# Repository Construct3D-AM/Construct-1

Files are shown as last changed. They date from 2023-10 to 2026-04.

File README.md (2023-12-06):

# README: Usage Guidelines
## Introduction
Welcome to the CAD Files Repository hosted by SERAPH TECHNOLOGIES t/a CONSTRUCT3D. This repository contains a collection of CAD, slicer and firmware files intended for educational and personal development purposes. We appreciate your interest and support in our work.

## Usage Restrictions
## 1. Non-Commercial Use Only
The CAD files provided in this repository are for **personal, non-commercial use only.** These files are not to be used for any commercial purposes, including but not limited to manufacturing, selling, or distribution of the designs or products derived from these files.

## 2. No Rights Granted
Downloading or using these CAD files **does not grant any rights or licenses to the user.** All rights, including but not limited to copyright, intellectual property rights, and distribution rights, are reserved by SERAPH TECHNOLOGIES. Any use of these files must comply with the terms and conditions stated herein.

## 3. Personal Use Only
The intent of providing these CAD files is solely for **personal use and learning.** Users are encouraged to use these files to enhance their skills, knowledge, and understanding of the relevant fields. However, any commercial exploitation or use of these files beyond personal purposes is strictly prohibited.

## 4. Modification and Redistribution
While users are permitted to modify the CAD files for personal use, redistribution of the original files or any modified versions is not allowed. Sharing these files on any platform or through any medium without the explicit permission of SERAPH TECHNOLOGIES is prohibited.

## 5. Disclaimer
SERAPH TECHNOLOGIES provides these CAD files 'as is' without any warranties, either expressed or implied. The use of these files is at the sole risk of the user. SERAPH TECHNOLOGIES shall not be liable for any direct, indirect, incidental, or consequential damages arising out of the use or inability to use these files.

## Acknowledgment
By downloading and using these CAD files, the user acknowledges that they have read, understood, and agreed to comply with the usage guidelines outlined in this document.

## Contact Information
For any inquiries or permissions related to the use of these CAD files, please contact SERAPH TECHNOLOGIES at:

[admin@construct-3d.com]

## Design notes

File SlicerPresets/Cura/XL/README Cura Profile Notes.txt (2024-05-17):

Notes: This document is temporary until the next update of CURA which hopefully will include our printers, natively.

=====
== Cura Setup Information
=====

=== Cura Setup instructions
You are going to want to add a 'Custom FFF machine'. this can be added under the preferences tab and adding a 'Non-networked printer".
In the scroll tab available, look for the 'Custom' header, and inside of the drop down, the 'Custom FFF printer' can be selected. You can name your printer what ever you deem fit. We personally use 'C1' or 'C1XL' as the machine designation, and then a custom name (like 'Dave') to indicate different machines.

=== Cura addons
It is recommended to instal a few 3rd party addons to your cura installation. These can be found by clicking the 'Marketplace' tab on the top.

We recommend:
Duet RepRapFirmware Integration:	This will provide the ability to send prints directly to the printers by adding the IP address to each printer

Arc Welder:		Adds the functionality to use G2 and G3 commands. Makes prints with curved surfaces MUCH prettier and faster.

PrintJob Naming:	Allows you to get rid of the annoying CFFF_xxx naming convention cura forces people to have.

Z offset Setting:	If everything is good, this isn't needed. However, in the case that the first layer print is not perfect, and you don't want to update the Z-probe offset in the printer, this can be a very simple way to update the z offset for first layer smoothness.

=== Printer tab
X (Width):		325
Y (Depth):		370
Z (Height):		400
Build plate shape:	Rectangular
Origin at center:	no
Heated bed:		Yes
Heated build volume:	no
G-code flavour:		RepRap

=== Printhead settings
X min:			-20
Y min:			-10
X max:			10
Y max:			10
Gantry Height:		100
Number of extruders:	1
Apply Extruder offsets to Gcode:	no

=== Extruder 1 Tab
Nozzle size:			0.6
Compatible material diameter:	1.75
Nozzle offset X:		0
Nozzle offset Y:		0
Cooling fan Number:		0

=== Start G-code
; Copy paste the following code into the Start G-Code text box

M106 S0 ; Turn Fan off
M190 S{material_bed_temperature_layer_0} ;Start heating bed
M109 S150
G28; home
G1 Z15 F6000 ; move the printer down 15mm
G1 Y2 F3000
M104 S{material_print_temperature_layer_0} ;Start heating extruder
M109 S{material_print_temperature_layer_0} ;Wait for extruder to reach temp before proceeding

;prime the extruder
G1 X5 Y2 Z0.3 F6000; go to edge of build volume
G1 X60 E10 F1000 ;gentle purge start
G1 X110 E25 F1000; heavy purge
G1 X60;
G92 E0

=== End G-code
; Copy paste the following code into the End G-Code text box

;Retract the filament
G92 E1
G1 E-5 F900
;Move nozzle fast
G1 X5 Y370 F15000
;Move Bed Down
G1 Z400 F6000

;Set machine to idle
M104 S0
M140 S0

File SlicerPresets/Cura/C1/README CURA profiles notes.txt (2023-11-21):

CURA profiles notes:

The profiles provided are still a work in progress. These will be updated regularly as feedback is provided to continually improve the performance of these profiles.
It is important to note that these profiles are currently set for PLA material. Please edit them as needed for other materials.

To install these presets, go to the 'preferences' tab at the top of the screen. then procede to the 'Profiles' tab and click 'Import' - please note the downloaded Zip file will need to be extracted first.

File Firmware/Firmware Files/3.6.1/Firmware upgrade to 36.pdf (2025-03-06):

## Firmware upgrade to 3.6.0 RC1

Changes in firmware can be found https://github.com/Duet3D/RepRapFirmware/releases/tag/3.6.0-rc.1 Release notes:
https://github.com/Duet3D/RepRapFirmware/wiki/Changelog-RRF-3.x-Beta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 (https://github.com/Duet3D/RepRapFirmware/wiki/Changelog-RRF-3.x-Beta)

Printer changes:
Fixed accuracy bug causing probe measurement points to offset by ~18mm from the correct location
Fixes to bed gantry levelling measurement point locations
New PanelDue Firmware for 3.6.x Compatibility and increased stability to DWC
New Homing Sequences
New machine build volume exclusion zone

Notes:
Release candidates can have unexpected new behaviours. Bugs and Errors are uncommon but not unforeseeable. To help with the development of the firmware, please take a full copy of the error code. And if the WebUI is accessible, Send M122 in the console and copy the output.

Step 1: Updating the Panel Due screen firmware
Download the Panel Due screen firmware from: https://github.com/Construct3D-AM/Construct-1/blob/master/Firmware/Panel%20Due/PanelDueFirmware.bin (https://github.com/Construct3D-AM/Construct-1/blob/master/Firmware/Panel%20Due/PanelDueFirmware.bin)

On the WebUI, locate the Firmware system Directory: /files/System/Firmware Directory

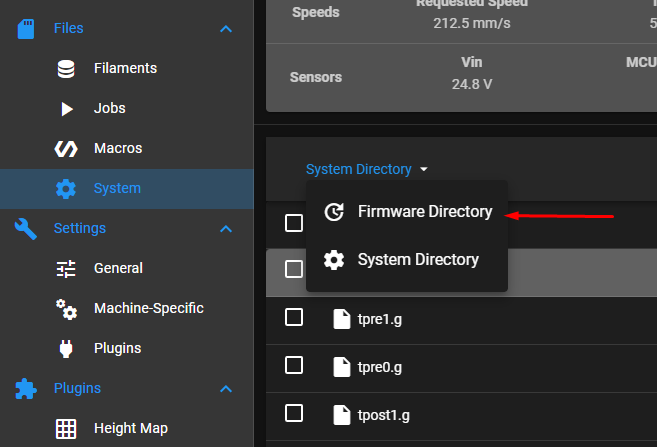
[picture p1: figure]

Upload the Panel Due firmware to the Firmware Directory and wait for the upload and install to complete.

Step 2: Updating the printer firmware
The firmware can be found here: https://github.com/Construct3D-AM/Construct-1/blob/master/Firmware/Firmware%20Files/3.6.beta/Beta4%20RC1/Duet2and3Firmw are-3.6.0-rc.1.zip (https://github.com/Construct3D-AM/Construct-1/blob/master/Firmware/Firmware%20Files/3.6.beta/Beta4%20RC1/Duet2and3Firmware-3.6.0-rc.1.zip)
In the Settings/Machine tab (machine specific) , you can update the entire machines firmware by simply installing the .Zip file from the GitHub Link

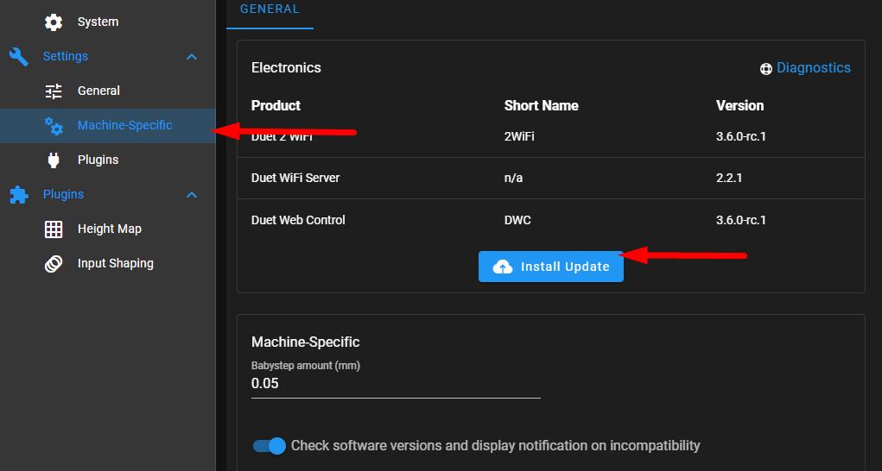
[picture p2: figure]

The printer will ask if you want to install the updates (including the wifi module if applicable), Press yes, and wait for the update to install. This can take a small while, so make sure not to turn the printer off during this process.

Step 3: System Config Changes
In Config.g please update the following:

Z probe X and Y values:

- G31 P800 X12 Y-26

Z-Probe Mesh Quality P value

- (C1 only) M557 P7
- (XL only) M557 P9

Axis Limits X and Y values:

- (C1 only) M208 X227 Y260
- (XL only) M208 X328 Y370

Input Shaping P and F values:

- M593 P"EI2" F45
(If the F value is above 35, then you can skip this stage)

Pressure Advance S value:

- M572 D0 S0.012
Step 4: Homing sequence changes
You can find the file directory here: https://github.com/Construct3D-AM/Construct-1/tree/master/Firmware/Config%20Files (https://github.com/Construct3D-AM/Construct-1/tree/master/Firmware/Config%20Files)
Replace the following files:
- Bed.g
- Homeall.g
- HomeX.g
- Homey.g

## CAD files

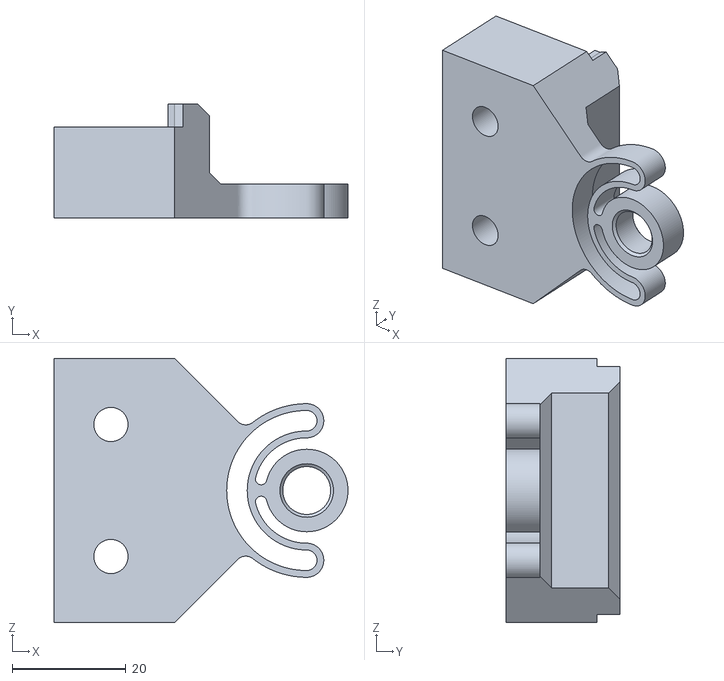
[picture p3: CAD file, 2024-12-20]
Cad Files/Ver 1.0 & 1.1/Printable Parts/Combined - All Parts/T8 Compliant Rod Clamp.stl
51.6 x 20.0 x 46.4

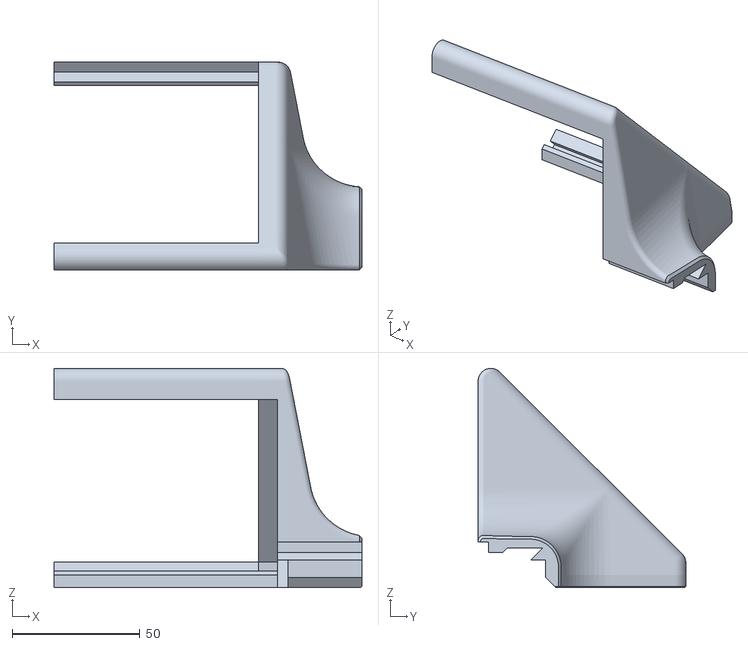
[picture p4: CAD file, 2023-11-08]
Cad Files/Ver 1.0 & 1.1/Printable Parts/Resin/Screen Right Surround V3.stl
120.4 x 81.3 x 85.7

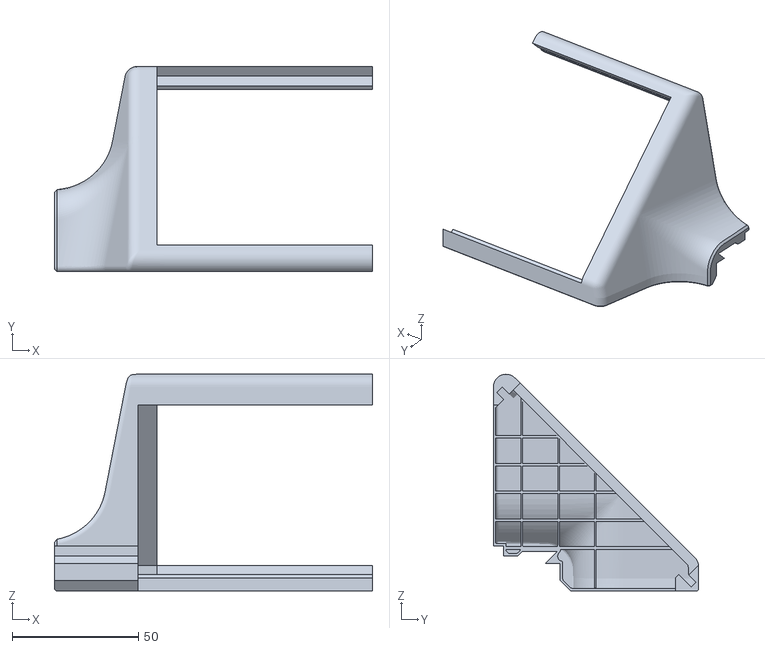
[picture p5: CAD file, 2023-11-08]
Cad Files/Ver 1.2+/Printable Parts/Resin/Screen Left Surround V3.stl
125.9 x 81.3 x 85.7

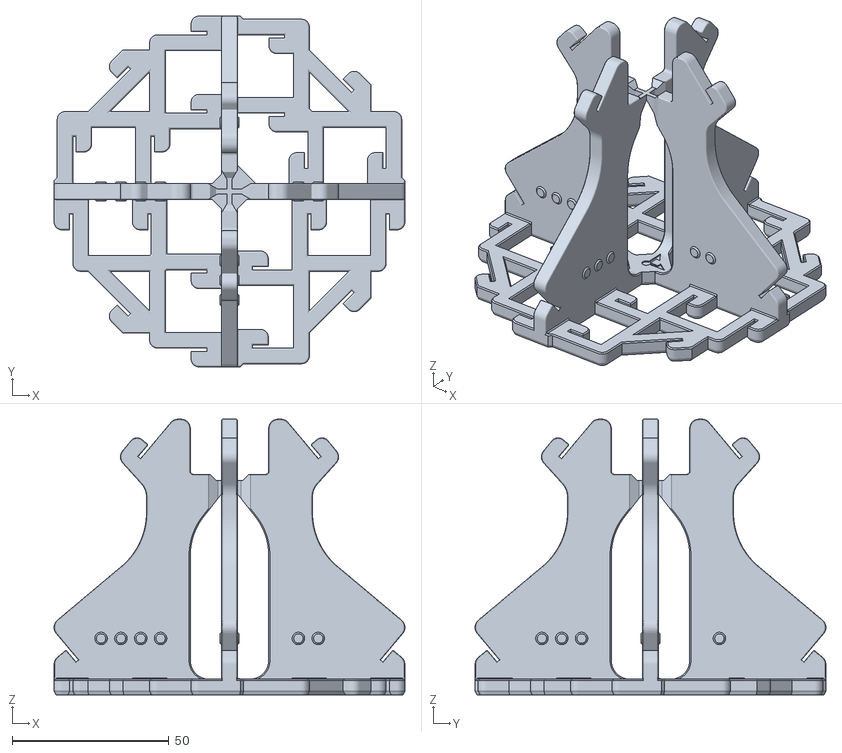
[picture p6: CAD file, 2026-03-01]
Compliance Print Files/Calilantern-100mm.stl
112.1 x 112.1 x 88.0

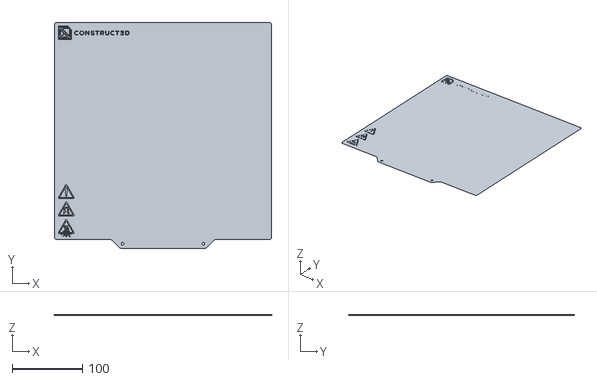
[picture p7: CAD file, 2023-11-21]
SlicerPresets/Orca/C1/Heater Bed 310x310 Orca.stl
310.0 x 322.7 x 0.5

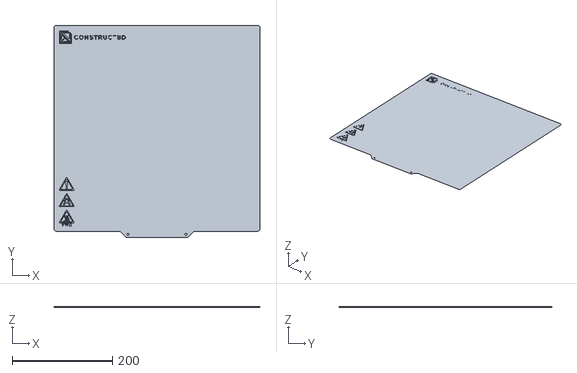
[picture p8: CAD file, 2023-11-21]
SlicerPresets/Orca/XL/Heater bed 410x410 Orca v3.stl
410.0 x 422.7 x 0.5

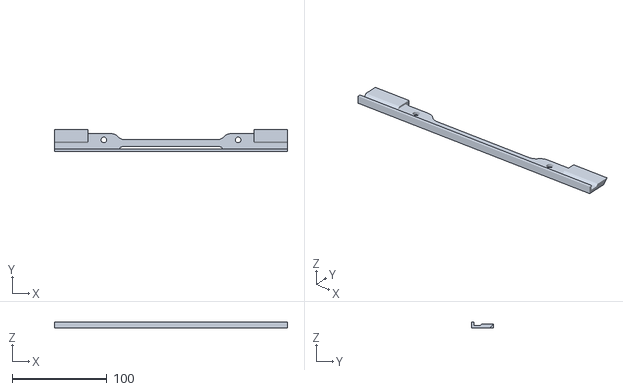
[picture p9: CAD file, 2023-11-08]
Cad Files/Ver 1.0 & 1.1/Printable Parts/Combined - All Parts/Screen French Cleat V3.stl
246.3 x 23.7 x 6.69

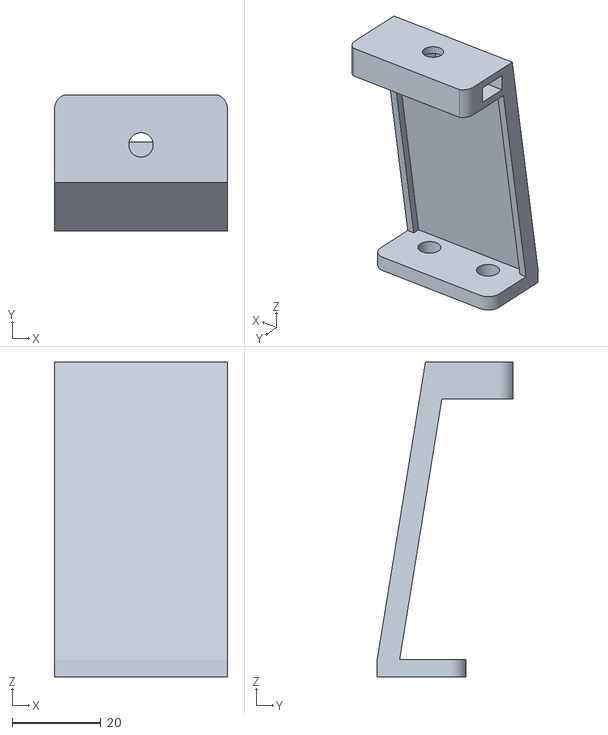
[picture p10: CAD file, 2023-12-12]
Cad Files/Ver 1.0 & 1.1/Printable Parts/Filament/XL Bottom bracket.stl
39.0 x 30.5 x 71.0

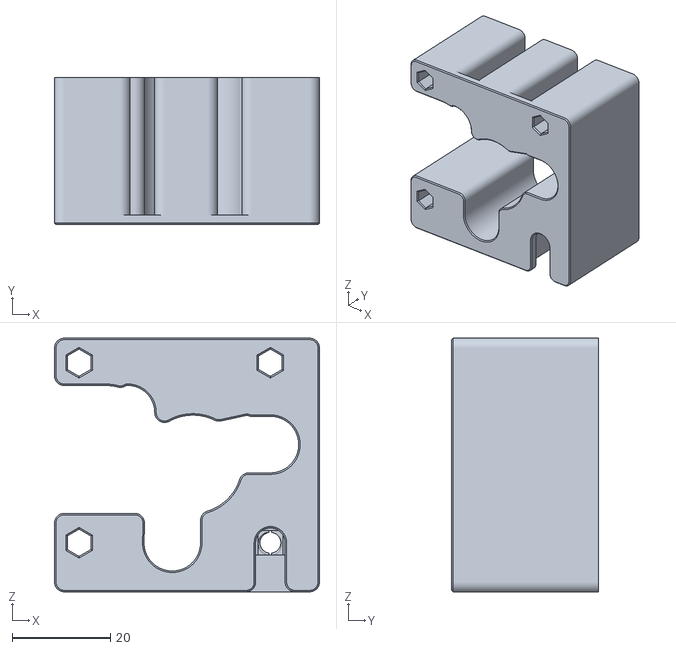
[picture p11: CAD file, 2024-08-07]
Cad Files/Ver 1.2+/Printable Parts/Combined - All Parts/Cage block spacer.stl
54.0 x 30.0 x 51.7

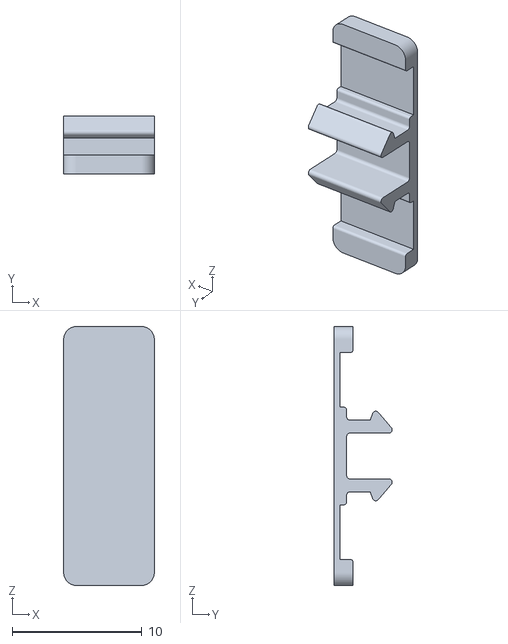
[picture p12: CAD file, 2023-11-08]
Cad Files/Ver 1.0 & 1.1/Printable Parts/Combined - All Parts/Wire Clips.stl
7.00 x 4.52 x 20.0

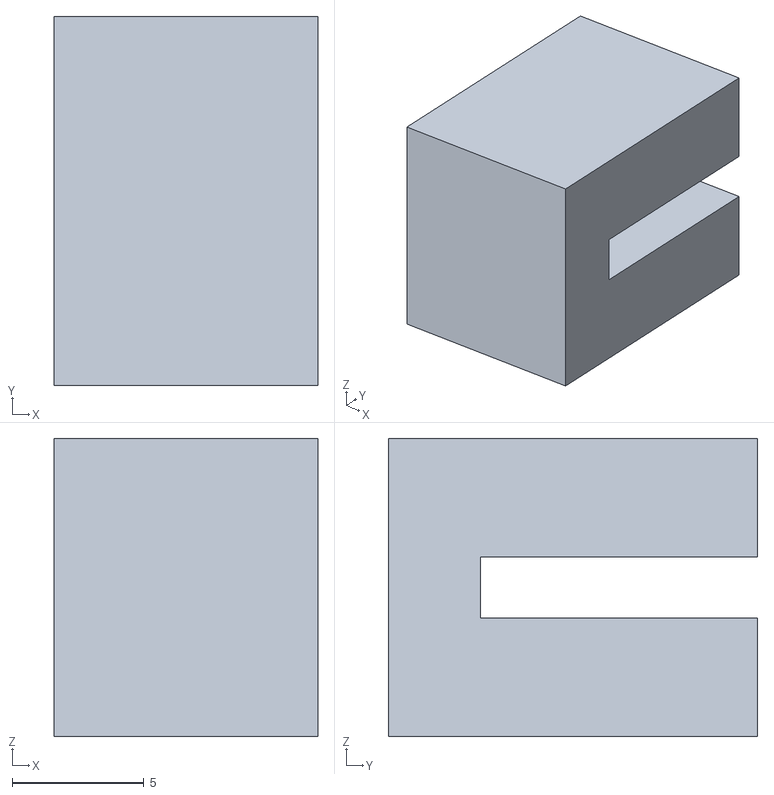
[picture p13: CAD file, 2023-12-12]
Cad Files/Ver 1.0 & 1.1/Printable Parts/Filament/Belt locking clip.stl
10.0 x 14.0 x 11.3

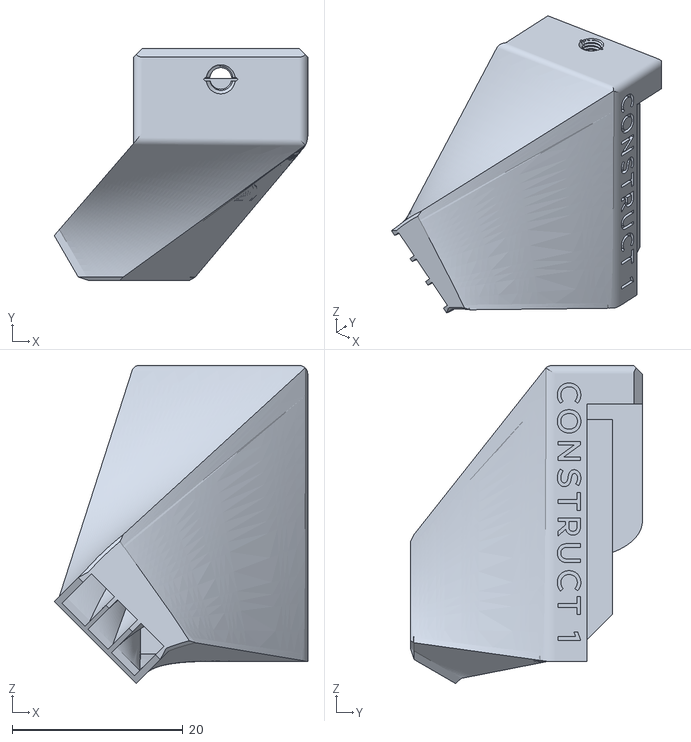
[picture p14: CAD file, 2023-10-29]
Cad Files/Ver 1.0 & 1.1/Printable Parts/Resin/Universal Front Fan Duct.stl
29.7 x 27.2 x 37.3

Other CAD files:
Cad Files/Ver 1.0 & 1.1/Printable Parts/Combined - All Parts/Probe Mount 8mm.stl
Cad Files/Ver 1.0 & 1.1/Printable Parts/Combined - All Parts/Screen Backplate.stl
Cad Files/Ver 1.0 & 1.1/Printable Parts/Combined - All Parts/Universal Rear Fan Duct.stl
Cad Files/Ver 1.0 & 1.1/Printable Parts/Filament/2020 corner bracket.stl
Cad Files/Ver 1.0 & 1.1/Printable Parts/Filament/French cleat.stl
Cad Files/Ver 1.0 & 1.1/Printable Parts/Filament/Screen Backplate.stl
Cad Files/Ver 1.0 & 1.1/Printable Parts/Filament/XL Corner Brace .stl
Cad Files/Ver 1.0 & 1.1/Printable Parts/Filament/XL Side bracket Left.stl
Cad Files/Ver 1.0 & 1.1/Printable Parts/Filament/XL Side bracket Right.stl
Cad Files/Ver 1.0 & 1.1/Printable Parts/Filament/XL Support Bracket.stl
Cad Files/Ver 1.0 & 1.1/Printable Parts/Resin/Probe Mount 8mm.stl
Cad Files/Ver 1.0 & 1.1/Printable Parts/Resin/Universal Rear Fan Duct.stl
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

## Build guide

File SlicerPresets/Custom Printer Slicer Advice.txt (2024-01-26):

For creating your own C1 and C1XL Print profiles, here is some advice for acheving best quality.

[TODO Add link to data source and reference images for quality vs agressiveness - find suitible host site for 105 high rez analysis photos]

1) When printing at 100mm/s vs 300mm/s, you can be much more agressive with the jerk and acceleration settings for 100mm/s.
2) For the C1 do not excede 25 mm/s Jerk values
3) For the C1XL do not excede 20mm/s Jerk values
4) For best quality accelerations, a value of 2800mm/s (C1) and 2400mm/s (XL)
5) For good quality accelerations, a value of 3600mm/s (C1) and 3400mm/s (XL)
6) For acceptable quality accelerations, a value of 4400mm/s (C1) and 4000mm/s (XL)
7) If you are experiencing noticable ringing on surfaces when printing at slow speeds (~60mm/s) this is an indicator that your belts are too tight. Release the tention by a single tooth, and this should resolve the artefact
8) Motor resonance speeds (commonly cause VFAs) are worse between 70mm/s and 120mm/s. This is not to say dont print at these speeds, but this will be more likely to see VFAs in print surfaces on glossy materials or if the belts are over tentioned
9) It is common for your home/factory intranet IP addresses to change suddenly at the whims of the router, this can cause a previously known IP for a printer to suddenly change, this may break any remote print send functionality untill it is identified and the new IP is set
10) The Vanadium nozzles are perfect for printing even the most abrasive materials, however they do cost between 10-20% flow headroom. This can be compensated by raising the temperature of the printed material by 8°C for the same flow rate
11) Construct 1 and Construct 1XL run the RepRapFirmware Flavour of G-Code
12) If you want to store images inside the GCode, the WebUI can show both QOI and PNG formats, The touch screen however can onyl show QOI - Please see Docs.Duet3d.com for the specifics on QOI image formatting

Have fun and happy printing.

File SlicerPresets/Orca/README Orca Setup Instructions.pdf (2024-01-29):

Notes: This document is temporary until the next update of ORCA which hopefully will include our printers, natively.
Step 1:
For Windows Users, download Orca Slicer: https://github.com/SoftFever/OrcaSlicer/releases/download/v1.9.0/OrcaSlicer_Windows_Installer_1.9.0.exe (If necessary copy and paste link into browser)

Other versions of OrcaSlicer can be found here: https://github.com/SoftFever/OrcaSlicer/releases/tag/v1.9.0

If the install does not automatically start, find the option to “keep” (see arrows on examples given below).

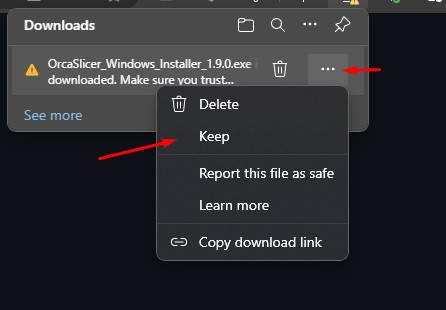
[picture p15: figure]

Step 2:
Run the installer.

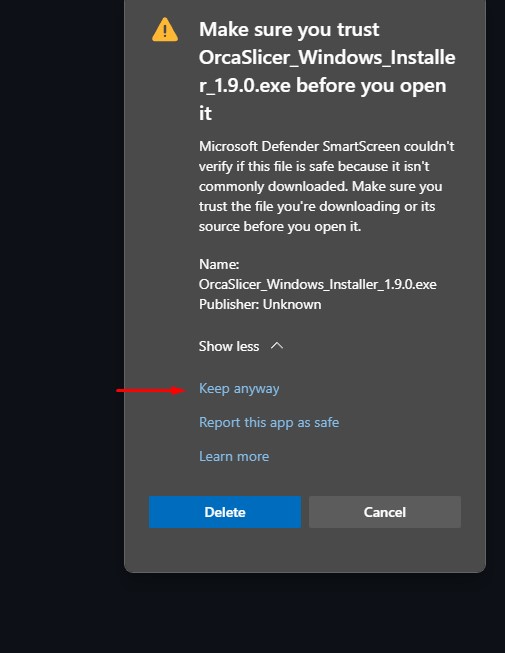
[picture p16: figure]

Step 3:
Open Orca Slicer
Step 4:
Download the profiles: https://github.com/Construct3D-AM/Construct-1/tree/master
To download the configs (+ all supporting files), click the green “code” button and then the Download Zip option.

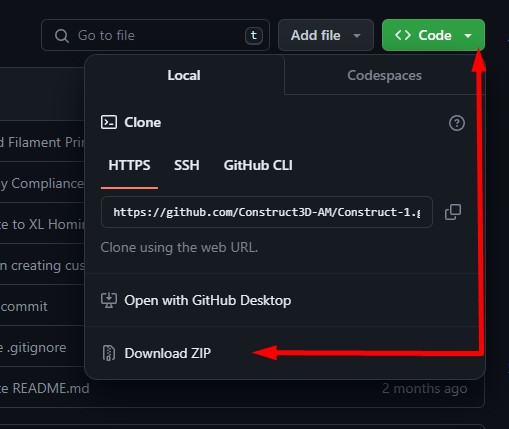
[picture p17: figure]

Proceed to Unzip the file.

Step 5:
Add the profiles:

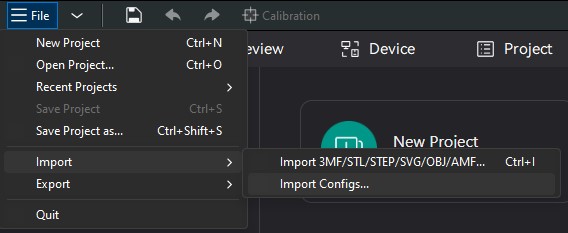
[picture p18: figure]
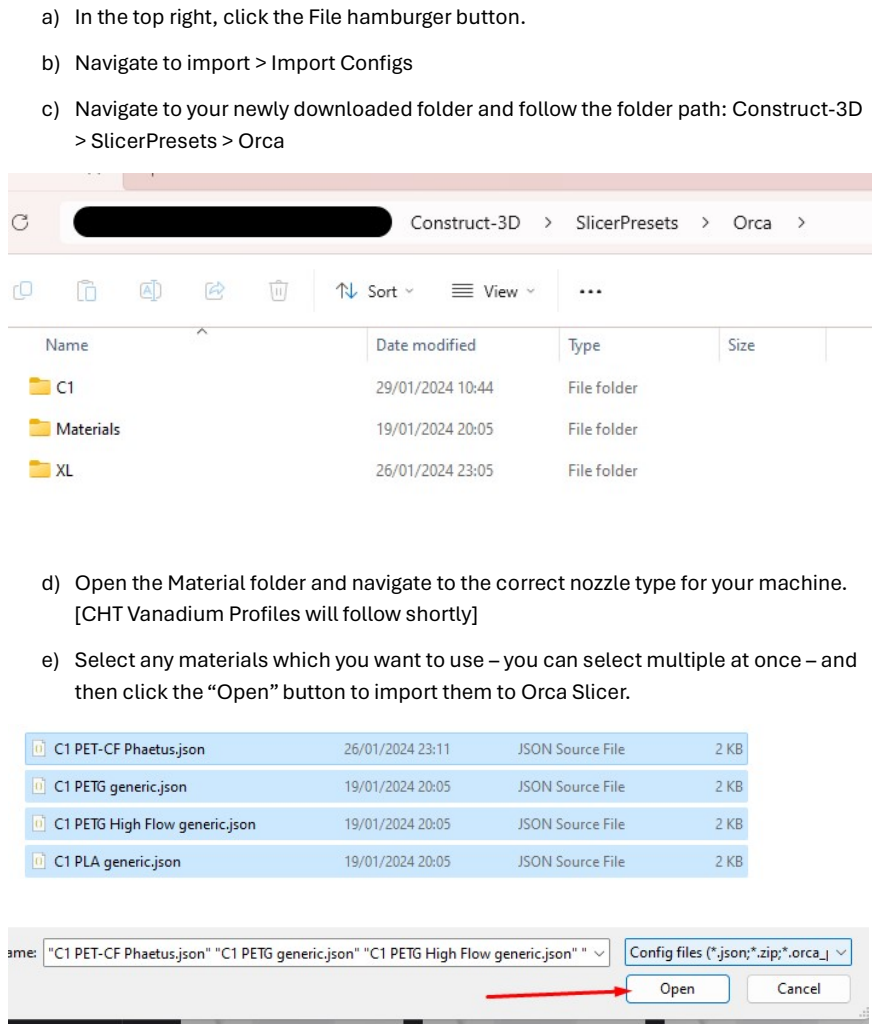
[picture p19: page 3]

a) In the top right, click the File hamburger button.
b) Navigate to import > Import Configs
c) Navigate to your newly downloaded folder and follow the folder path: Construct-3D > SlicerPresets > Orca
d) Open the Material folder and navigate to the correct nozzle type for your machine. [CHT Vanadium Profiles will follow shortly]
e) Select any materials which you want to use – you can select multiple at once – and then click the “Open” button to import them to Orca Slicer.

f) In Orca Slicer, add the printer by going to File>import>Configs> etc. and navigate to the correct folder for your machine. (See example using an XL printer below)
g) Open the “Printer” folder, select the “Construct 1 XL.json” file and open it.

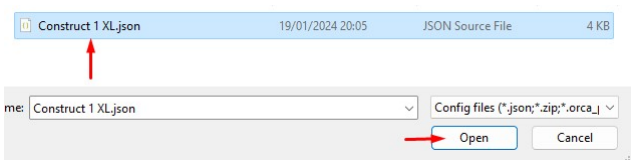
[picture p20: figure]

h) The printer has now been successfully added to the slicer.
Next we can add the print profiles, these tell the slicer how to create printer files that best suit the machine to achieve higher quality than the default profiles provided.
i) In Orca Slicer, select File>Import>Import Configs> and navigate to the “Process” folder (Construct-3D > SlicerPresets > Orca > XL > Process)

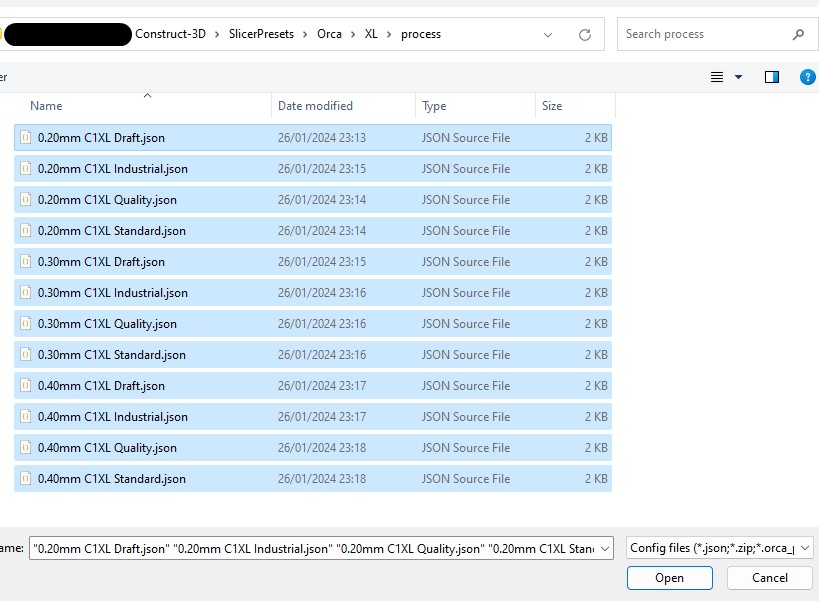
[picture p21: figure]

j) Once all the files have been selected you can click “Open”. This will import all the print profiles to Orca Slicer.
Step 6:
Orca Slicer now has all the relevant information for CONSTRUCT3D printers. Next, set them up as the default.
Proceed to the “prepare” tab in Orca

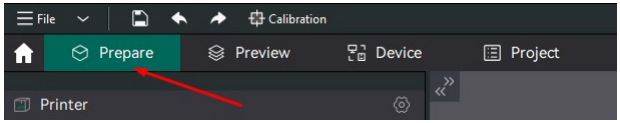
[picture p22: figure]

Under the “printer segment” there will be a drop down box. This may currently say “MyMarlin”. Click the drop down box and select your printer. (See example below)

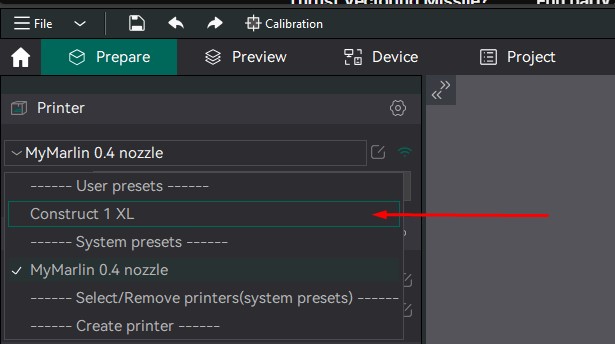
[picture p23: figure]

Select filament: Below the “Printer” tab, there is a “Filament” tab.
Click its corresponding dropdown and select one of the preset filaments. The example below is for PLA.

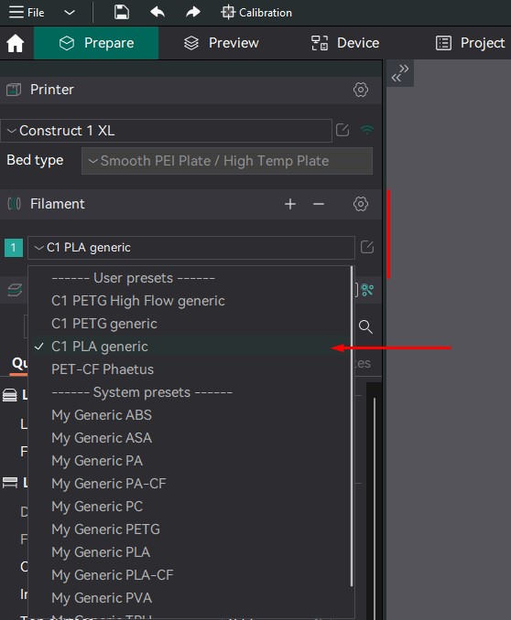
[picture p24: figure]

Select a print profile.
The example below is for a 0.3mm profile for the XL

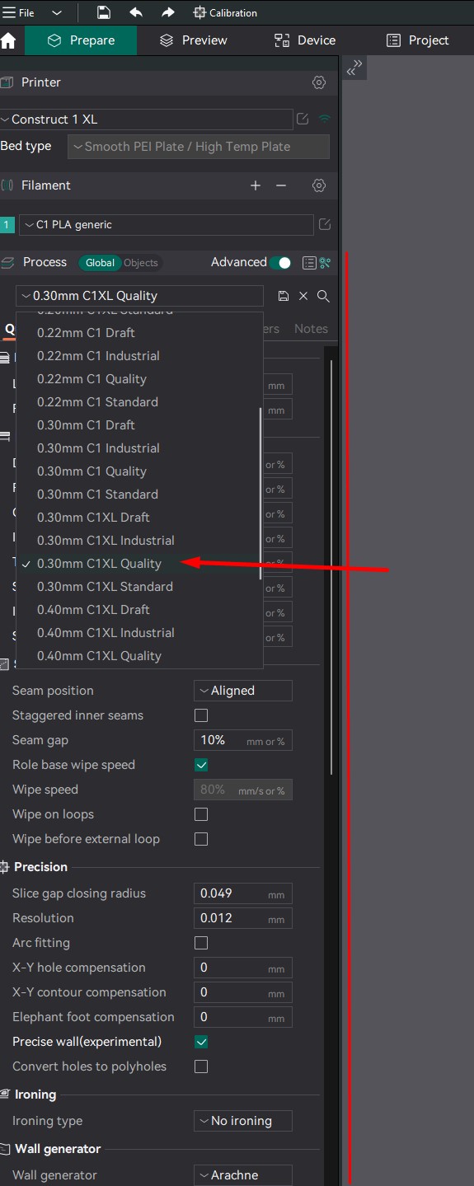
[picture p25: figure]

Behind the dropdown for the preset are the inidividual settings that are included in the profile.
The presets automatically update these settings so depending on how much granular control over the slicing process, you are free to modify these.

Step 7:
i) Importing the 3D model for the build platform.
ii) Telling the slicer the printer’s IP for remote print sending.
i) Orca should be displaying the current build volume as a grid in the centre of the screen. To update the build volume to accurately represent the printer bed:
a) click the options button next to the printer’s name.

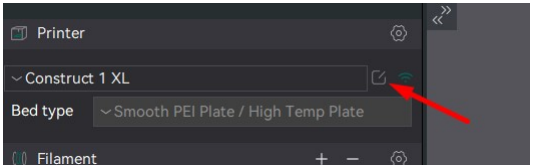
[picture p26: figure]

b) click the “Set printable area” button in the new dialog box

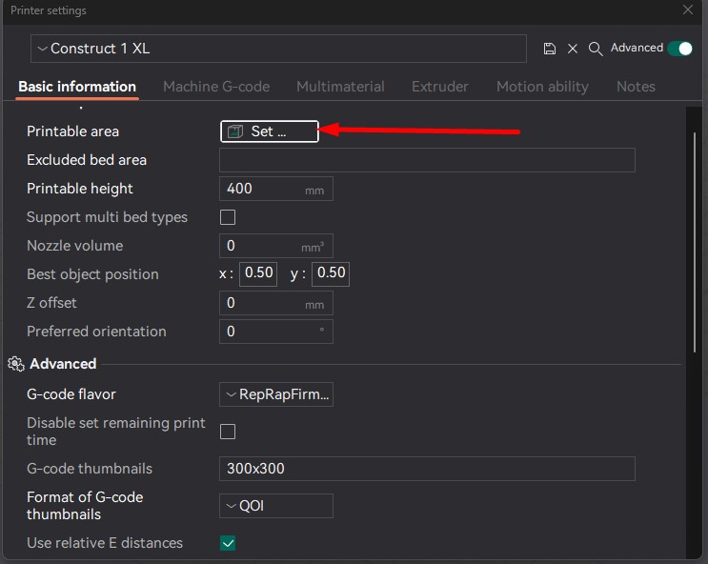
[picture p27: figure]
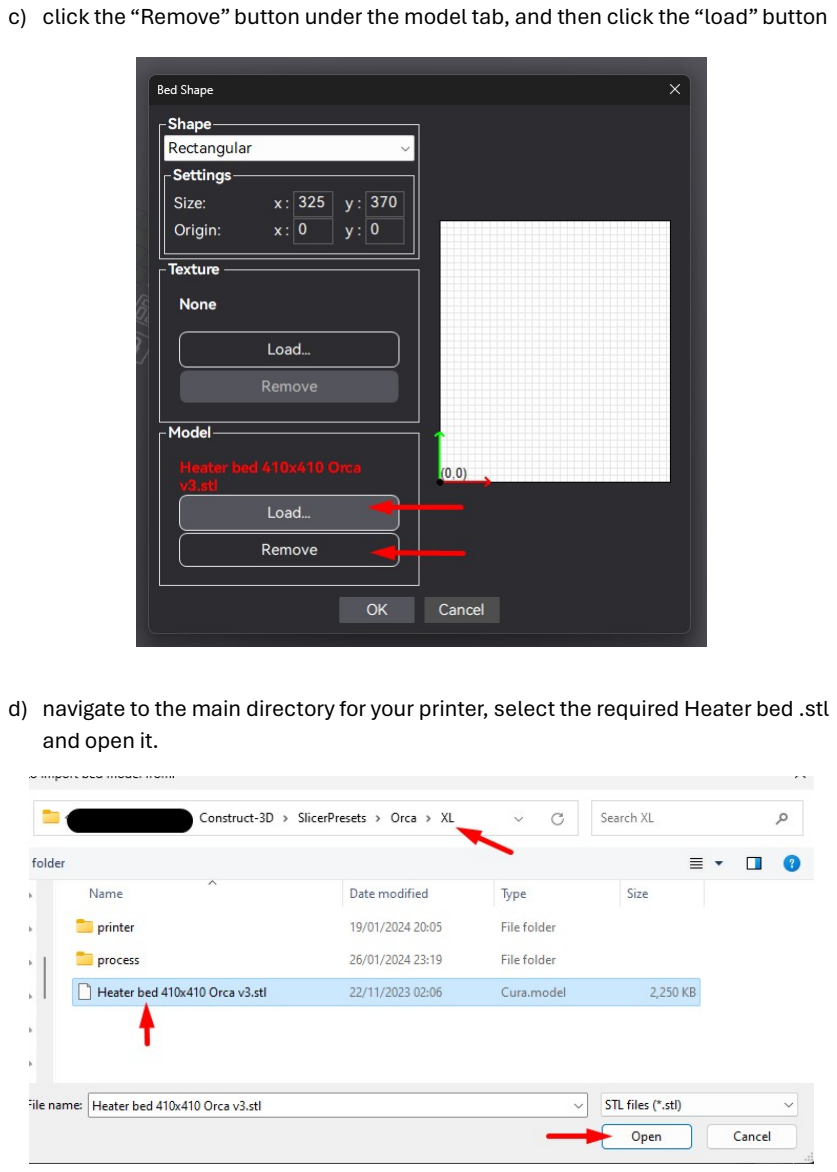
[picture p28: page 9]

c) click the “Remove” button under the model tab, and then click the “load” button
d) navigate to the main directory for your printer, select the required Heater bed .stl and open it.

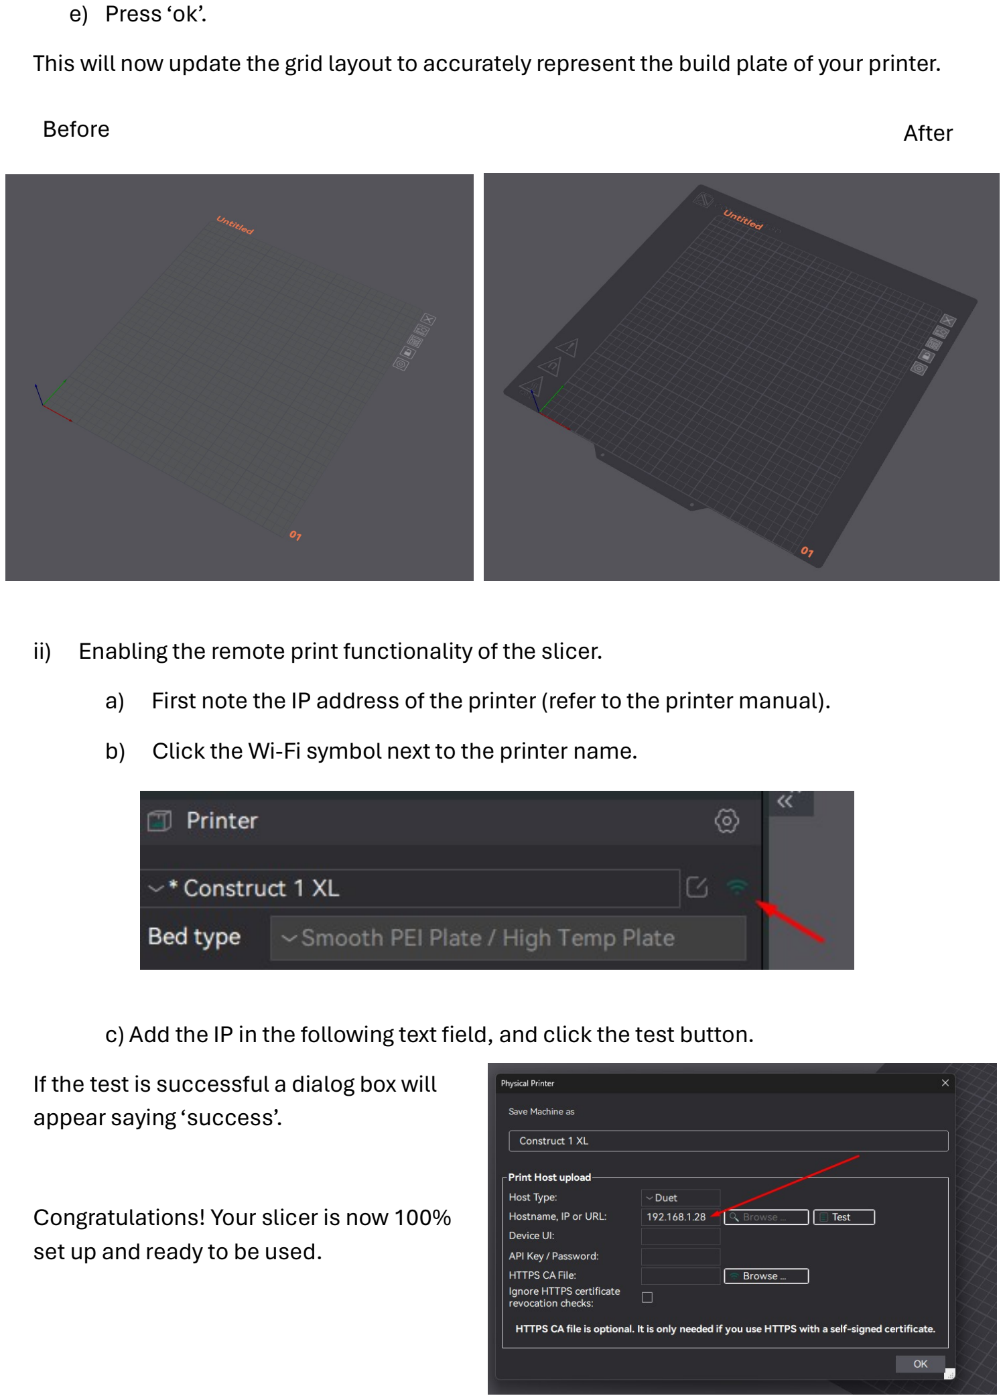
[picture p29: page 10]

e) Press ‘ok’.
This will now update the grid layout to accurately represent the build plate of your printer.

ii) Enabling the remote print functionality of the slicer.
a) First note the IP address of the printer (refer to the printer manual).
b) Click the Wi-Fi symbol next to the printer name.
c) Add the IP in the following text field, and click the test button. If the test is successful a dialog box will
appear saying ‘success’.

Congratulations! Your slicer is now 100% set up and ready to be used.

Before | After

NOTE:

Please remember that the print profiles provided are intentionally generic to be a great starting point for almost any material or model. These printers can perform even better when you have a good understanding of what material you are using and what your model requires for optimum slicer settings.

Once you are comfortable with how the printer works, feel free to play around with the slicer settings. Happy printing!

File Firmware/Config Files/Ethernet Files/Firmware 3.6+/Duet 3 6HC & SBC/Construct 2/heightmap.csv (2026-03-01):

RepRapFirmware height map file v2 generated at 2026-02-20 17:19 | min error 0.045 | max error 0.424 | mean 0.247 | deviation 0.093
axis0 | axis1 | min0 | max0 | min1 | max1 | radius | spacing0 | spacing1 | num0 | num1
X | Y | 82.00 | 255.64 | 91.39 | 296.99 | -1.00 | 11.00 | 11.00 | 16 | 19
0.045 | 0.064 | 0.083 | 0.094 | 0.119 | 0.145 | 0.152 | 0.159 | 0.170 | 0.181 | 0.188 | 0.184 | 0.184 | 0.181 | 0.170 | 0
0 | 0.071 | 0.086 | 0.112 | 0.134 | 0.152 | 0.156 | 0.174 | 0.174 | 0.177 | 0.184 | 0.188 | 0.184 | 0.184 | 0.174 | 0.152
0.049 | 0.060 | 0.086 | 0.105 | 0.119 | 0.141 | 0.148 | 0.152 | 0.156 | 0.163 | 0.174 | 0.170 | 0.170 | 0.163 | 0.148 | 0
0 | 0.075 | 0.094 | 0.119 | 0.130 | 0.148 | 0.156 | 0.159 | 0.170 | 0.177 | 0.177 | 0.184 | 0.181 | 0.174 | 0.159 | 0.141
0.060 | 0.086 | 0.097 | 0.123 | 0.141 | 0.159 | 0.163 | 0.163 | 0.174 | 0.184 | 0.184 | 0.192 | 0.184 | 0.177 | 0.170 | 0
0 | 0.105 | 0.119 | 0.148 | 0.163 | 0.174 | 0.188 | 0.188 | 0.192 | 0.199 | 0.206 | 0.202 | 0.195 | 0.184 | 0.184 | 0.163
0.097 | 0.127 | 0.141 | 0.159 | 0.181 | 0.188 | 0.199 | 0.199 | 0.206 | 0.224 | 0.220 | 0.216 | 0.216 | 0.213 | 0.202 | 0
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

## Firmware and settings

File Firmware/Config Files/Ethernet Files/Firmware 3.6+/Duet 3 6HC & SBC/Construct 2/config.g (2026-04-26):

;█
;   _____ ____  _   _  _____ _______ _____  _    _  _____ _______     ____  _____  
;  / ____/ __ \| \ | |/ ____|__   __|  __ \| |  | |/ ____|__   __|   |___ \|  __ \ 
; | |   | |  | |  \| | (___    | |  | |__) | |  | | |       | |        __) | |  | |
; | |   | |  | | . ` |\___ \   | |  |  _  /| |  | | |       | |       |__ <| |  | |
; | |___| |__| | |\  |____) |  | |  | | \ \| |__| | |____   | |       ___) | |__| |
;  \_____\____/|_| \_|_____/   |_|  |_|  \_\\____/ \_____|  |_|      |____/|_____/ 
;                                                                                

;███████████████████████████████████████████████████████████████████████████████████
;General Setup
M575 P1 S1 B57600                                                     ; enable support for PanelDue
G90                                                                   ; send absolute coordinates...
M83                                                                   ; ...but relative extruder moves
M550 P"C1E"                                                           ; set printer name
M669 K1                                                               ; select CoreXY mode

;███████████████████████████████████████████████████████████████████████████████████
;Tertiary
M950 E0 C"led" T1 U20 Q3000000   ;set strips and Q=Signal frequency
M150 E0 R40 U40 B255 P255 S20 ;Auto set to llight blue on startup

; Wait a moment for the CAN expansion boards to start
G4 S5

;███████████████████████████████████████████████████████████████████████████████████
;Drive setup
; D3    D4    D5
; XYl   N/A   XYr
;
; D2    D1    D0
; Zl    N/A   Zr

M569 P0.3 S1                                                          ; XYl motor physical drive goes forwards
M569 P0.5 S1                                                          ; XYr motor physical drive goes forwards
M569 P0.2 S1                                                          ; zl motor physical drive goes forwards
M569 P0.0 S1                                                          ; zr motor physical drive goes forwards
M569 P121.0 S0                                                        ; ToolBoard Extruder motor physical drive goes backwards

M584 X0.2 Y0.5 Z0.0:0.3 E121.0                                        ; set drive mapping
M350 X32 Y32 Z16 I1                                                   ; configure microstepping with interpolation
M350 E16 I1
M92 X160 Y160 Z800 E410                                              ;Set steps per/mm

;███████████████████████████████████████████████████████████████████████████████████
;Drive Control
M566 X1200 Y1200 Z400 E300                                         ; set maximum instantaneous speed changes (mm/min)
M203 X50000 Y50000 Z1800 E3000.00                                    ; set maximum speeds (mm/min)  - 500mm/s XY
M201 X20000 Y20000 Z500 E10000                                         ; set accelerations (mm/s^2)
M201.1 X600 Y600 Z300
M906 X3950 Y3950 Z850 E1200 I80                                        ; set motor currents (mA) and motor idle factor in per cent
M84 S30                                                               ; Set idle timeout

; Stall detection Values
M915 X Y S3 F0 H100 

;███████████████████████████████████████████████████████████████████████████████████
;Printer Control
; Axis Limits
M208 X0 Y0 Z0 S1                                                      ; set axis minima
M208 X340 Y390 Z400 S0                                                ; set axis maxima

; Endstops
M574 X1 S3                                                            ; configure sensorless endstop for low end on X
M574 Y2 S3                                                            ; configure sensorless endstop for high end on Y

;Duet Scanning Zprobe (Eddy current)
M558 K1 P11 C"121.i2c.ldc1612" F450:200:14000 T14000 A3 H5:H1
M308 A"SZP coil" S10 Y"thermistor" P"121.temp2"                       ; thermistor on coil
G31 K1 P6400 Z2 X17 Y11.5
M558.2 K1 S13 R138974                                                 ;measured at 2.5mm from nozzle against bed Z0
M558.3 K1 S0 H-0.25 V1.8 F450                                                ;Set touch mode operations but disable(S0) touch for now
M557 X20:330 Y30:360 S11


;Toolboard Accelerometer
M955 P121.0 I01                                                       ; Add accelerometer on Roto with CAN address 121 and specify orientation

;Independent Z leveling
M671 X-10:340 Y190:190 S10                                            ; leadscrews locations at left (connected to Z) and right (connected to E1) of X axis

;███████████████████████████████████████████████████████████████████████████████████
;Heater Control
;each gets
;M308 A thermistor maped to a sensor
;M950 Heater is created on sensor output
;M307 Heater type is catagorised
;M140 or M141 to say if bed or chamber
;M143 to configure max temp

G4 S1 ; wait for board
;nozzle heater
M308 S1 P"121.temp1" Y"pt1000" A"Nozzle"                              ; configure sensor 1 as thermistor on pin temp1
M950 H1 C"121.out0" T1                                                ; create heater and map sensor 1 (toolboard)
M307 H1 R2.346 K0.580:0.000 D3.78 E1.35 S1.00 B0 V25.0                ; Disable Bang Bang
M143 H1 S360                                                          ;set max temp
;bed heater
M308 S0 P"0.temp0" Y"thermistor" A"Bed" T100000 B3950                 ; configure sensor 0 as thermistor on pin temp1
M950 H0 C"out9" T0                                                    ; create bed heater output on out1 and map it to sensor 0
M307 H0 R0.593 K0.350:0.000 D3.19 E1.35 S1.00 B0                      ; disable bang-bang mode for the bed heater and set PWM limit
M140 H0                                                               ; map heated bed to heater 0
M143 H0 S130                                                          ;set max temp
;chamber heater
M308 S2 P"temp3" Y"thermistor" A"Chamber" T100000 B4267 C7.06e-8      ; configure sensor 2 as thermistor on pin temp2    
M950 H2 C"out0" T2                                                    ;Create chamber heater on out0 (Normally bed output) and map it to temp0 on mainboard
M307 H2 R0.7 K2.772:0.000 D15 E1.35 S1.00 B1                          ;disable bang bang and configure heate
M141 H2                                                               ; Set as chamber heater
M143 H2 S80                                                           ; Set max temp
M570 H2 P1500 T20                                                      ;Set weakened heater fault detection as heater is MUCH slower to react to power changes P=time before fault T=temp detla allowance


;Heatsink ambient sensor
;M308 S3 P"121.temp0" Y"thermistor" A"Heatsink" T100000 B4267 C7.06e-8 ; configure sensor 2 as thermistor on pin temp2 on TOOLBOARD

;Electronic chamber sensor 
M308 S4 P"temp2" Y"thermistor" A"Electronics Chamber" T100000 B4267 C7.06e-8

;Chamber Sensor Top
M308 S5 P"temp1" Y"thermistor" A"Chamber Top" T100000 B4267 C7.06e-8      ; configure sensor 2 as thermistor on pin temp2    


;███████████████████████████████████████████████████████████████████████████████████
;Fan Control


;nozzle heatsink
M950 F0 C"121.out1" Q500
M106 P0 S0 B0.5 C"Nozzle Fan"                                             ;Thermostatically controlled (35C+) Heatsink fan on out1 on Toolboard

;User Controlable
;M950 F1 C"121.out2" Q1000                                               ;Part cooling fan (5V) on Toolboard
;M106 P1 S0 L65 X255 H-1 B0.1                                            ;later date replace with tacho equipped 5v

;Chamber Fans
M950 F4 C"!out4+out4.tach"                                              ;Chamber 12032 fans connected to 4 wire on mainboard
M950 F5 C"!out5+out5.tach"
M950 F6 C"!out6+out6.tach"
M950 F7 C"!out7+io7.in"                                                 ;Chamber 12032 fans connected to 2 wire output and io7 as input for tach on mainboard

;Exhaust fans
M950 F8 C"out8"                                                         ;Exhaust fan with carbon filter
M106 P8 S255 B0.5 H5 T70 C"Exhaust Fan"                                 ;Set thermostatic control to 50C


;███████████████████████████████████████████████████████████████████████████████████
;Tools
M563 P0 S"Nozzle" D0 H1 F0                                            ;Create tool0 called heater using the first extruder (0) in the list using heater 1 and fan 1
G10 P0 X0 Y0 Z0 R0 S0                                                 ;set active and standby to 0
T0                                                                    ;choose tool 0 as default
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

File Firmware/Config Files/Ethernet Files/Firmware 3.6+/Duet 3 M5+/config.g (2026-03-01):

;   _____ ____  _   _  _____ _______ _____  _    _  _____ _______     ____  _____  
;  / ____/ __ \| \ | |/ ____|__   __|  __ \| |  | |/ ____|__   __|   |___ \|  __ \ 
; | |   | |  | |  \| | (___    | |  | |__) | |  | | |       | |        __) | |  | |
; | |   | |  | | . ` |\___ \   | |  |  _  /| |  | | |       | |       |__ <| |  | |
; | |___| |__| | |\  |____) |  | |  | | \ \| |__| | |____   | |       ___) | |__| |
;  \_____\____/|_| \_|_____/   |_|  |_|  \_\\____/ \_____|  |_|      |____/|_____/ 
;                                                                                

;███████████████████████████████████████████████████████████████████████████████████
;General Setup
M575 P1 S1 B57600                                      ; enable support for PanelDue
G90                                                    ; send absolute coordinates...
M83                                                    ; ...but relative extruder moves
M550 P"Construct 1 XL"                                            ; set printer name
M669 K1                                                ; select CoreXY mode


; Enable network
if {network.interfaces[0].type = "ethernet"}
    M552 S1
else
    M552 S1

;███████████████████████████████████████████████████████████████████████████████████
;Drive setup
M569 P0.0 S1                                           ; extruder motor physical drive goes forwards
M569 P0.1 S0 D2                                        ; XYr motor physical drive goes forwards
M569 P0.2 S0 D2                                        ; XYl motor physical drive goes forwards
M569 P0.3 S1 D2                                          ; Zr motor physical drive goes forwards
M569 P0.4 S1 D2                                          ; Zl motor physical drive goes forwards


M584 X0.1 Y0.2 Z0.3:0.4 E0.0                           ; set drive mapping
M350 X16 Y16 Z16 I1                                    ; configure microstepping with interpolation
M350 E16 I1
M92 X80 Y80 Z800 E397                                  ;Set steps per/mm

;███████████████████████████████████████████████████████████████████████████████████
;Drive Control
M566 X2000 Y2000 Z40 E500.00                          ; set maximum instantaneous speed changes (mm/min)
M203 X30000 Y30000 Z1500 E30000.00                     ; set maximum speeds (mm/min)  - 500mm/s XY
M201 X10000 Y10000 Z300 E5000                          ; set accelerations (mm/s^2)
M906 X1700 Y1700 Z850 E1200 I50                        ; set motor currents (mA) and motor idle factor in per cent
M84 S30                                                ; Set idle timeout

; Stall detection Values
M915 P0.1:0.2 S8 F0 H100 

;███████████████████████████████████████████████████████████████████████████████████
;Printer Control
; Axis Limits
M208 X0 Y0 Z0 S1                                       ; set axis minima
M208 X328 Y360 Z400 S0                                 ; set axis maxima

; Endstops
M574 X1 S3                                             ; configure sensorless endstop for low end on X
M574 Y2 S3                                             ; configure sensorless endstop for high end on Y
M574 Z1 S1 P"121.io0.in"                                            ; configure z-probe endstop active high

; P+F Z-Probe
M558 K0 P8 C"io6.in" H3:2 F600:100 A3 T12000         ; disable Z probe but set dive height, probe speed and travel speed
M557 X15:300 Y30:330 P7                                ; define mesh grid
G31 K0 P800 X12 Y-26 Z1.88                                 ; set Z probe trigger value, offset and trigger height

;Independent Z leveling
M671 X-10:340 Y190:190 S10                             ; leadscrews locations at left (connected to Z) and right (connected to E1) of X axis

;███████████████████████████████████████████████████████████████████████████████████
;Heater Control

;nozzle heater
M308 S1 P"0.temp2" Y"thermistor" A"Nozzle"             ; configure sensor 1 as thermistor on pin temp1
M950 H1 C"0.out1" T1                                   ; create heater and map sensor 1 (toolboard)
M307 H1 R1.974 K0.387:0.000 D5.45 E1.35 S1.00 B0 V24.9 ; Disable Bang Bang
M143 H1 S340                                           ;set max temp
;bed heater
M308 S0 P"0.temp0" Y"thermistor" A"Bed" T100000 B3950  ; configure sensor 0 as thermistor on pin temp1
M950 H0 C"0.out0" T0                                   ; create bed heater output on out1 and map it to sensor 0
M307 H0 R0.591 K0.268:0.000 D3.07 E1.35 S1.00 B0       ; disable bang-bang mode for the bed heater and set PWM limit
M140 H0                                                ; map heated bed to heater 0
M143 H0 S130                                           ;set max temp

;███████████████████████████████████████████████████████████████████████████████████
;Fan Control

M950 F0 C"out5" Q500                                   ; create fan 0 on pin fan0 and set its frequency
M106 P0 S0 H-1                                         ; set fan 0 value. Thermostatic control is turned off
M950 F1 C"out6" Q500                                   ; create fan 1 on pin fan1 and set its frequency
M106 P1 S0 H-1                                         ; set fan 1 value. Thermostatic control is turned off

;███████████████████████████████████████████████████████████████████████████████████
;Tools
M563 P0 S"Nozzle" D0 H1 F0:1                           ;Create tool0 called heater using the first extruder (0) in the list using heater 1 and fan 1
G10 P0 X0 Y0 Z0 R0 S0                                  ;set active and standby to 0
T0

;███████████████████████████████████████████████████████████████████████████████████
;Quality enchancements
M593 P"EI2" F45 S0.01                                  ; input shaping
M572 D0 S0.012                                         ; pressure advance
M309 S0.022 P0                                         ; material feedforward

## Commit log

2023-10-21 Create Probe Mount 8mm.stl
    [Probe Mount 8mm.stl]
2023-10-29 Added Resin printable fan ducts
    [Universal Front Fan Duct.stl, Universal Rear Fan Duct.stl]
2023-11-08 CAD and Printable parts update
    Added full CAD file for XL printer, and updated the printable parts library to include the majority of all finished designs.
    [Probe Mount 8mm.stl, Screen Backplate.stl, Screen French Cleat V3.stl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]
2023-11-21 Added Slicer Profiles - OrcaSlicer
    Slicer profiles added for Orca Slicer
    Included are setup files for C1 and XL
    [Heater bed 410x410 Orca v3.stl, Orca_310_x_310_PEI_bed_model_v1.stl]
2023-11-21 Update to C1 PLA generic material Orca Profile
    Bed temps corrected to actual intended values
2023-11-21 Cura Slicer Presets C1 & XL
    Printer profiles for Curaslicer.
    Including C1 and XL.
2023-11-21 Printer Firmware Added
    Printer firmware a config gcode added.
    Includes files for C1, C1XL, C1ethernet, C1XLethernet
    [bed.g, cancel.g, config.g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]
2023-12-06 Improved all homing files (Drastically)
    Refactored homeall.g to call inidividual home#.g files instead of hard coded homing sequences.
    Fixed "Z-probe already triggered" error, printer now automatically lowers bed if bed is detected too close to the nozle before a homing sequence.
    Updated XL print volume to remove any chance of hotend fan colliding on right side of printer
    Updated XL homing sequence to fix sensorless homing accuracy error causing left side of extruder (cooling fan) to collide with linear rod clamps
    [config.g, homeall.g, homex.g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]
2023-12-06 Heater Feedforward Added
    Adds a small amount of heater feedforward which will improve nozzle temperature stability in high flow print moves
    [config.g]
2023-12-06 Increased Max Nozzle Temp
    [config.g]
2023-12-07 Benchy Compliance prints added
2023-12-12 Added Filament Printable STLs
    [2020 corner bracket.stl, Belt locking clip.stl, Compliant t8 Rod clamp.stl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]
2024-01-17 Fixed Typo in Config.G files
    [config.g]
2024-01-19 New FIlament Profiles Added
    Removed old profiles and replaced with new flow optimized versions
2024-01-19 Orca - Added New XL Print Profiles
    New materials, Print profiles, and printer settings for orca
2024-01-25 Added placeholder C1 Print Profiles for Orca
2024-01-26 Reworked Material folder structure
    [Heater Bed 310x310 Orca.stl]
2024-01-28 Update to XL Homing Squence
    Minor update to the sequence of XL homing to make the process much more reliable
    [homeall.g, homey.g]
2024-01-29 Updated flow of Orca setup process
2024-02-07 Typo in file names fixed
    [Screen Left Surround V3.stl]
2024-04-19 Updated C1 Homing Sequence
    Updated the C1 homing parameters to include a 3mm safety margin in the left side.
    This will stop any risk of sensorless homing inaccuracies causing the fan duct to clip the left axial rods
    [config.g, homeall.g, homex.g]
2024-06-22 C1 V1.2 files added
    [2020 corner bracket.stl, Belt locking clip.stl, Compliant t8 Rod clamp.stl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]
2024-06-25 Printable presliced files added
    [Back mesh digital weave.stl, C1 Mesh Bottom Bracket Right.stl, C1 mesh bottom bracket left.stl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]
2024-07-03 Updated XL Benchy compliance print
2024-07-18 Updated printable files for XL v1.2
    [Back mesh digital weave.stl, XL Bottom Mesh Bracket Left.stl, XL Bottom Mesh Bracket Right.stl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]
2024-07-18 Updated printable files for XL backs
    [XL Top bracket.stl]
2024-07-24 Added Wobble X printable parts
    [WobbleX Bottom.stl]
2024-07-24 C1 back brackets STL added
    [C1 Side bracket double.stl, C1 Side bracket single.stl, C1 top bracket.stl]
2024-08-05 Create Instillation instructions updating printer firmware to 3.6.0alpha2+3.pdf
2024-08-07 added cage block spacer CAD
    [Cage block spacer.stl]
2024-12-20 Firmware and T8 CAD updates
    [Compliant t8 Rod clamp.stl, T8 Compliant Rod Clamp.stl, XL Compliant Rod clamp .stl]
2025-02-27 Create Assembly manual XL V1.1.pdf
2025-02-28 Added printer configs for FW3.6+
    [bed.g, cancel.g, config.g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]
2025-03-06 Re organised file structure to include 3.6 firmware
    [bed.g, cancel.g, config.g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]
2025-03-06 FW 3.6 Config changes
    [config.g]
2025-03-06 Bed.g FW3.6 updates
    [bed.g]
2025-04-05 C1 Mesh homing update
    [config.g]
2025-04-05 Mesh level update
    [config.g]
2025-05-30 Updated max Jerk to match print profiles
    [config.g]
2025-06-19 added vanadium configs
    [config.g]
2025-06-19 updated 3.6 C1 ethernet config
    [config.g]
2025-06-25 Create Benchy Compliance Print Vanadium.gcode
2026-02-03 Compliance prints update
2026-02-03 Added Duet3m5+ config
    [bed.g, cancel.g, config.g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]
2026-03-01 Duet35+ added to firmware config
    [Calilantern-100mm.stl, bed.g, cancel.g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]
2026-03-01 CONSTRUCT 2 Config Files Added
    [bed.g, cancel.g, config.g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]
2026-04-26 C2 firmware update
    [config.g]
